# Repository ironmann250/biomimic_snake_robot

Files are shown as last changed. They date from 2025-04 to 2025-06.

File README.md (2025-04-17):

# biomimic_snake_robot
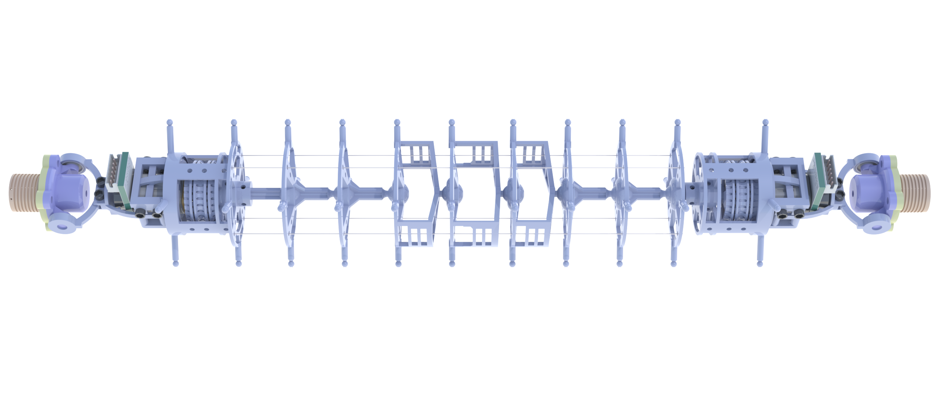
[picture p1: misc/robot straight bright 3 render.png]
biomimic_snake_robot render


CAD, PCB and Code files for an under actuated snake robot made to mimic snakes.

# Requirements
- Solidworks v2022
- python v3.8+ (anaconda packages)
- arduino (esp32 arduino api v3+)
- for V1 PCB code use stm32cubeide or similar ARM Dev IDE(like keil)
- EasyEDA PRO (PCB design)

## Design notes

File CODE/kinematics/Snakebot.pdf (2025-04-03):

# Snakebonnnnt

Munyakabera Jean Claude

September 2024

## 1 Definitions

S = Number of Segments
θn = Relative angle of segment n
Θn = Absolute angle of segment n
Cn = Center (base) point of segment n Ln = Left point of segment n
Rn = Right point of segment n
W = Width of segment from center to edge H = Height of segment from center to top X = Cord displacement (per segment)

Rot(

a
b

, θ) =
cosθ −sinθ

sinθ cosθ a b

(1)

=

a · cosθ − b · sinθ

a · sinθ + b · cosθ
(2)

## 2 Models

Θn =

X

S

i=0

θi | (3)

Cn+1 = Cn + Rot(

0
H
, Θn) | (4)

Ln = Cn − Rot(

W
0
, Θn) | (5)

Rn = Cn + Rot(

W
0
, Θn) | (6)

1

## 3 Initial Conditions

C0 =

0
0
(7)
θ0 = 0 | (8)

L0 = C0 − Rot(

W
0

, Θ0) =
−W
0
(9)

R0 = C0 + Rot(

W
0

, Θ0) =
W
0
(10)

C1 = C0 + Rot(

0
H

, Θ0) =
0
H
(11)

L1 = C1 − Rot(

W
0

, Θ) =
−W · cosΘ
H − W · sinΘ
(12)

R1 = C1 + Rot(

W
0

, Θ) =
W · cosΘ
H + W · sinΘ
(13)

## 4 Inverse solution

Let Θ = Θ1 for readability, then

∥L1 − L0∥2 = H − X | (14)
∥R1 − R0∥2 = H + X | (15)
∥R1 − R0∥2 = ∥L1 − L0∥ + 2X | (16)
W · cosΘ − W
H + W · sinΘ

2

=

W − W · cosΘ
H − W · sinΘ

2

+ 2X

p
(W · cosΘ − W)
2 + (H + W · sinΘ)² = | (17)
p
(W − W · cosΘ)² + (H − W · sinΘ)² + 2X | (18)

Apply two approximations for small angles:

cos(θ) = 1 −

θ

2
2

(19)

sin(θ) = θ | (20)
r
W² Θ⁴
4
+ H² + W²Θ² + 2HWΘ = | (21)
r
W² Θ⁴
4

+ H² + W²Θ² − 2HWΘ + 2X

2

Simplify further and remove terms that are negligible at small angles:

p

H² + 2HWΘ = p
H² − 2HWΘ + 2X | (22)

H² + 2HWΘ = H² − 2HWΘ + 4X(X +

p
H² − 2HWΘ) (23)

4HWΘ = 4X(X +

p
H² − 2HWΘ) | (24)
HWΘ ≈ X(X + H) | (25)

Θ ≈

X(X + H)
W H

(26)

3

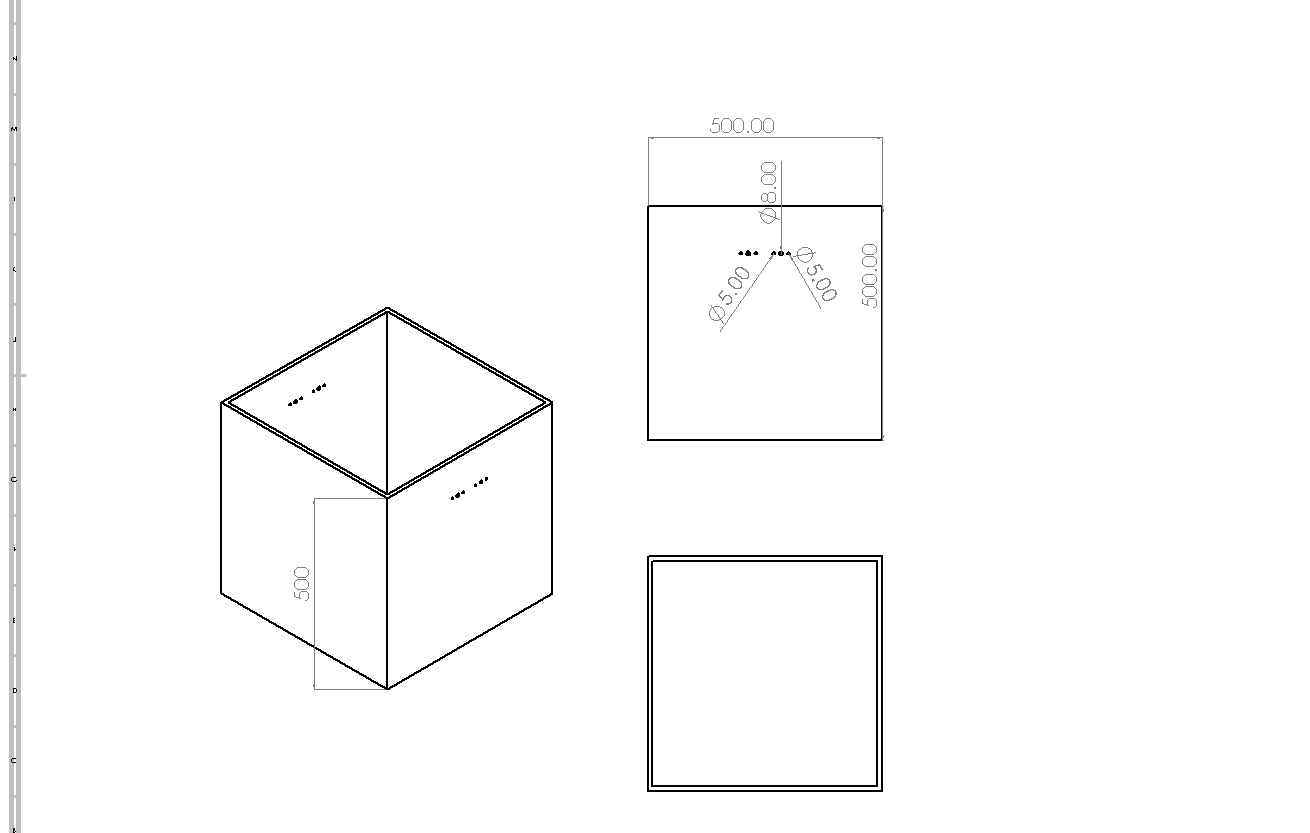
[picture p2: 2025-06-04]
CAD/V3/acrylic cube.TIF

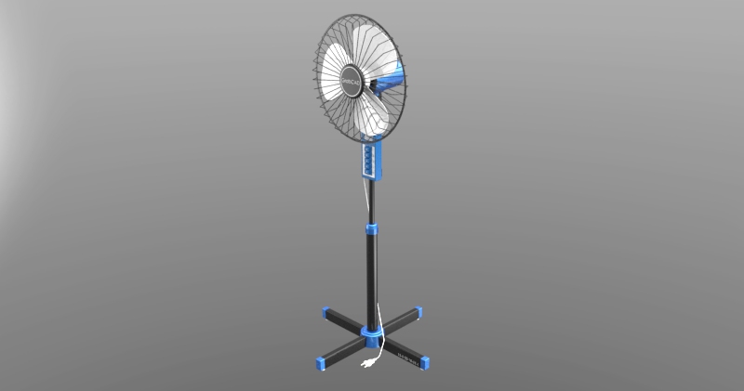
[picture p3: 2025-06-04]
CAD/V3/stand-fan-4/Sobni Ventilator (Rendering ).jpg

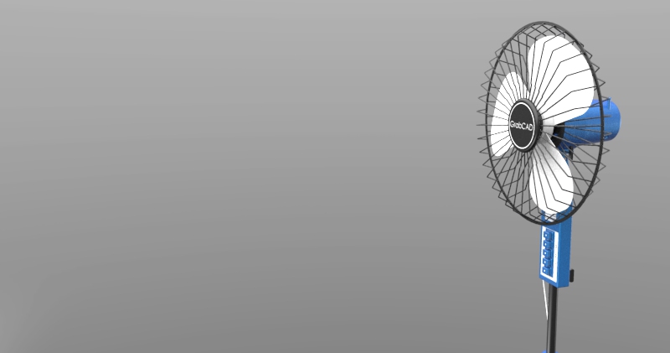
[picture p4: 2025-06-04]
CAD/V3/stand-fan-4/Sobni Ventilator (Rendering 4 ).jpg

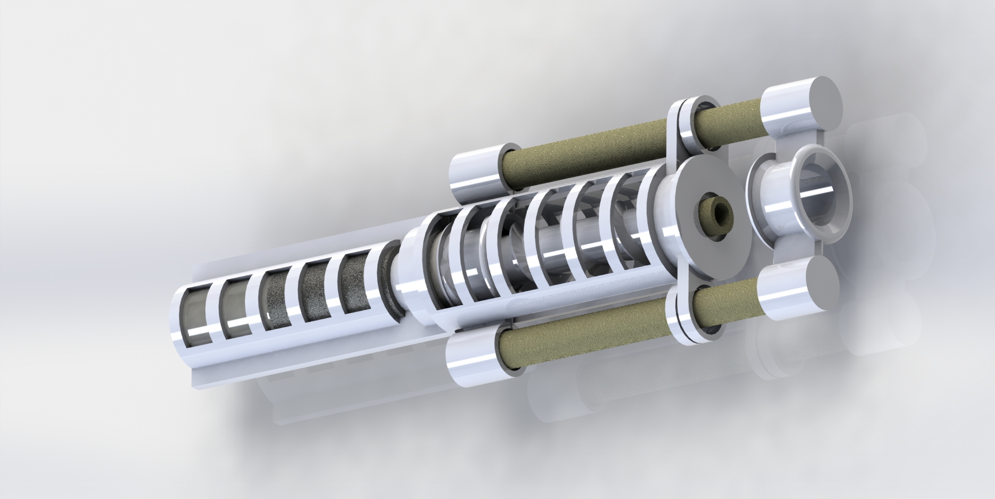
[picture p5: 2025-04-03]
CAD/modular version/linear motor render.JPG

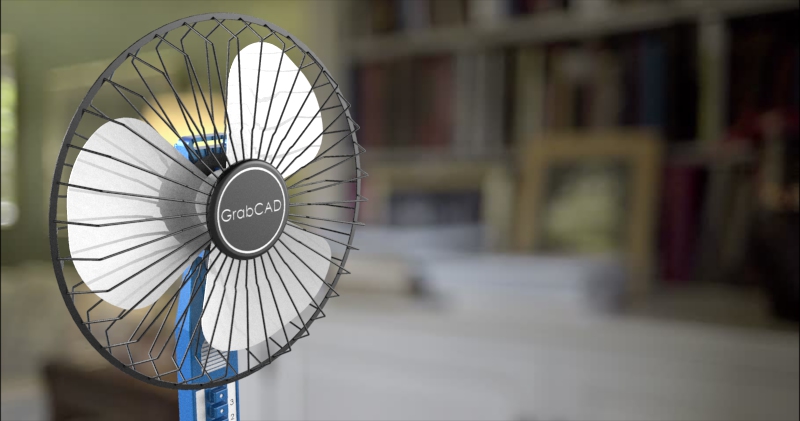
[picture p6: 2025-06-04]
CAD/V3/stand-fan-4/Sobni Ventilator (Rendering 3).jpg

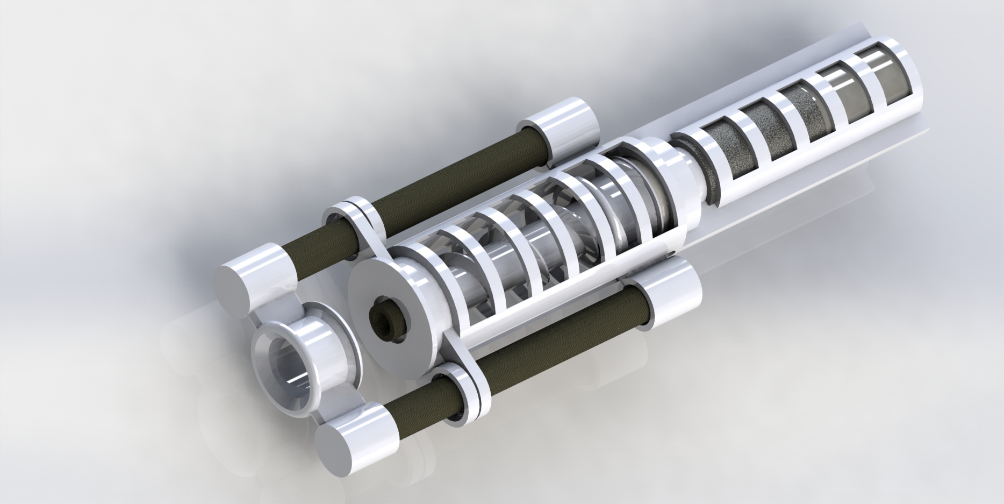
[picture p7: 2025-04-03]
CAD/modular version/linear motor render2.JPG

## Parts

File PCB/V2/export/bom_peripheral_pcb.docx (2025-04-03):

No. | Quantity | Comment | Designator | Footprint | Value | Manufacturer Part | Manufacturer | Supplier Part | Supplier
1 | 2 | 0.1uF | C1, C3 | C0603 | 0.1uF
2 | 4 | 10uF | C2, C4, C5, C6 | C0603 | 10uF
3 | 1 | DF40C-40DP-0.4V(51) | CN1_female1 | CONN-SMD_DF40C-40DP-0.4V | | DF40C-40DP-0.4V(51) | HRS(广濑) | C424643 | LCSC
4 | 1 | PMEG2010EPK,315 | D1 | SOD1608_L1.6-W0.8-LS1.6-RD | | PMEG2010EPK,315 | Nexperia(安世) | C552829 | LCSC
5 | 1 | AFC01-S08FCA-00 | FPC3 | FPC-SMD_P0.50-8P_FGS-XJ-H2.0 | | AFC01-S08FCA-00 | JS(钜硕电子) | C262657 | LCSC
6 | 1 | XL-1005UGC_C2856703 | LED1 | LED0402-RD_GREEN | | XL-1005UGC | XINGLIGHT(成兴光) | C2856703 | LCSC
7 | 1 | IRLML6401TRPBF | Q2 | SOT-23-3_L2.9-W1.3-P1.90-LS2.4-BR | | IRLML6401TRPBF | TECH PUBLIC(台舟) | C5182042 | LCSC
8 | 2 | IRLML6244TRPBF | Q5, Q6 | SOT-23-3_L2.9-W1.3-P1.90-LS2.4-BR | | IRLML6244TRPBF | Infineon(英飞凌) | C143946 | LCSC
9 | 1 | 5.1k | R1 | R0603 | 5.1k
10 | 1 | 4.7K | R3 | R0402 | 4.7k | RC0402FR-0710KL | YAGEO(国巨) | C60490 | LCSC
11 | 2 | 10K | R4, R5 | R0603 | 10K
12 | 2 | 1TS015A-1500-0600-CT | SW1, SW2 | SW-SMD_L3.0-W2.0-LS3.5 | | 1TS015A-1500-0600-CT | HYP(鸿源精密) | C319434 | LCSC
13 | 1 | DOUBLE_DRV8210 | U2 | DOUBLE_DRV8210
14 | 1 | SGM2212-3.3XKC3G/TR | U5 | SOT-223-4_L6.5-W3.5-P2.30-LS7.0-BR | | SGM2212-3.3XKC3G/TR | | C9900018517 | LCSC
15 | 1 | RED LED | U6 | LED0402-R-RD | | RED LED | YONGYUTAI(永裕泰) | C20608784 | LCSC
16 | 1 | MicroQTJ | USB1 | MICRO-USB-SMD_MICROQTJ-5P | | MicroQTJ | SHOU HAN(首韩) | C404968 | LCSC

BILL OF MATERIALS: PERIPHERAL PCB

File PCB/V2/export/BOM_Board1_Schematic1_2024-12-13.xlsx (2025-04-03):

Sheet: bom模板
 |  |  |  | Bill of Materials | BOM_Board1_Schematic1_2024-12-13
 |  |  |  | Project Title： | new pcb design
 |  |  |  | Variant:
 |  |  |  | Report Time： | 2024年12月13日 15:29:9
No. | Quantity | Comment | Designator | Footprint | Value | Manufacturer Part | Manufacturer | Supplier Part | Supplier | buy | solder
1 | 20 | Test-Point | 3V3, ADC1, ADC2, AO1, AO2, BO1, BO2, COM_5V, GND1, GND2, GND3, HEAT1, HEAT2, PWM4, RXD0, SCL1, SDA1, TXD0, VBAT, VM | Test-Point-0.5mm |  |  |  |  |  | 0 | û
2 | 2 | 0.1uF | C1, C3 | C0603 | 0.1uF |  |  |  |  | 30 | ü
3 | 4 | 10uF | C2, C4, C5, C6 | C0603 | 10uF |  |  |  |  | 50 | ü
4 | 1 | DF40C-40DP-0.4V(51) | CN1_female1 | CONN-SMD_DF40C-40DP-0.4V |  | DF40C-40DP-0.4V(51) | HRS(广濑) | C424643 | LCSC | 0 | ü
5 | 1 | PMEG2010EPK,315 | D1 | SOD1608_L1.6-W0.8-LS1.6-RD |  | PMEG2010EPK,315 | Nexperia(安世) | C552829 | LCSC | 0 | ü
6 | 1 | AFC01-S08FCA-00 | FPC3 | FPC-SMD_P0.50-8P_FGS-XJ-H2.0 |  | AFC01-S08FCA-00 | JS(钜硕电子) | C262657 | LCSC | 15 | ü
7 | 1 | XL-1005UGC_C2856703 | LED1 | LED0402-RD_GREEN |  | XL-1005UGC | XINGLIGHT(成兴光) | C2856703 | LCSC | 15 | ü
8 | 1 | IRLML6401TRPBF | Q2 | SOT-23-3_L2.9-W1.3-P1.90-LS2.4-BR |  | IRLML6401TRPBF | TECH PUBLIC(台舟) | C5182042 | LCSC | 0 | ü
9 | 2 | IRLML6244TRPBF | Q5, Q6 | SOT-23-3_L2.9-W1.3-P1.90-LS2.4-BR |  | IRLML6244TRPBF | Infineon(英飞凌) | C143946 | LCSC | 0 | ü
10 | 1 | 5.1k | R1 | R0603 | 5.1k |  |  |  |  | 15 | ü
11 | 1 | 4.7K | R3 | R0402 |  | RC0402FR-0710KL | YAGEO(国巨) | C60490 | LCSC | 15 | ü
12 | 2 | 10K | R4, R5 | R0603 | 10K |  |  |  |  | 25 | ü
13 | 2 | 1TS015A-1500-0600-CT | SW1, SW2 | SW-SMD_L3.0-W2.0-LS3.5 |  | 1TS015A-1500-0600-CT | HYP(鸿源精密) | C319434 | LCSC | 0 | ü
14 | 1 | DOUBLE_DRV8210 | U2 | DOUBLE_DRV8210 |  |  |  |  |  | 0 | û
15 | 1 | SGM2212-3.3XKC3G/TR | U5 | SOT-223-4_L6.5-W3.5-P2.30-LS7.0-BR |  | SGM2212-3.3XKC3G/TR |  | C9900018517 | LCSC | 0 | ü
16 | 1 | RED LED | U6 | LED0402-R-RD |  | RED LED | YONGYUTAI(永裕泰) | C20608784 | LCSC | 15 | ü
17 | 1 | MicroQTJ | USB1 | MICRO-USB-SMD_MICROQTJ-5P |  | MicroQTJ | SHOU HAN(首韩) | C404968 | LCSC | 0 | ü

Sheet: Field汇总
Project Title | new pcb design
Borard Title | Board1
Schematic Title | Schematic1
PCB Title
Variant Name
Total Quantity | 43
Report Time | 15:29:9
Report Date | 2024年12月13日
Report Date&Time | 2024年12月13日 15:29:9
File Name | BOM_Board1_Schematic1_2024-12-13
Filter Option | <Parameter filter option not found>

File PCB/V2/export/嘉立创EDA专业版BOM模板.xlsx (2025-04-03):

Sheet: bom模板
 |  |  |  | Bill of Materials | Field=File Name
 |  |  |  | Project Title： | Field=Project Title
 |  |  |  | Variant: | Field=Variant Name
 |  |  |  | Report Time： | Field=ReportDateTime
No. | Column=Quantity | Column=Comment | Column=Designator | Column=Footprint | Column=Value | Column=Manufacturer Part | Column=Manufacturer | Column=Supplier Part | Column=Supplier | Column=LCSC Price | Total
1 |  |  |  |  |  |  |  |  |  |  | ¥0.00
2 |  |  |  |  |  |  |  |  |  |  | ¥0.00
3 |  |  |  |  |  |  |  |  |  |  | ¥0.00
4 | ¥0.00

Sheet: Field汇总
Project Title | Field=Project Title
Borard Title | Field=Borard Title
Schematic Title | Field=Schematic Title
PCB Title | Field=PCB Title
Variant Name | Field=Variant Name
Total Quantity | Field=Total Quantity
Report Time | Field=Report Time
Report Date | Field=Report Date
Report Date&Time | Field=ReportDateTime
File Name | Field=File Name
Filter Option | Field=Filter Option

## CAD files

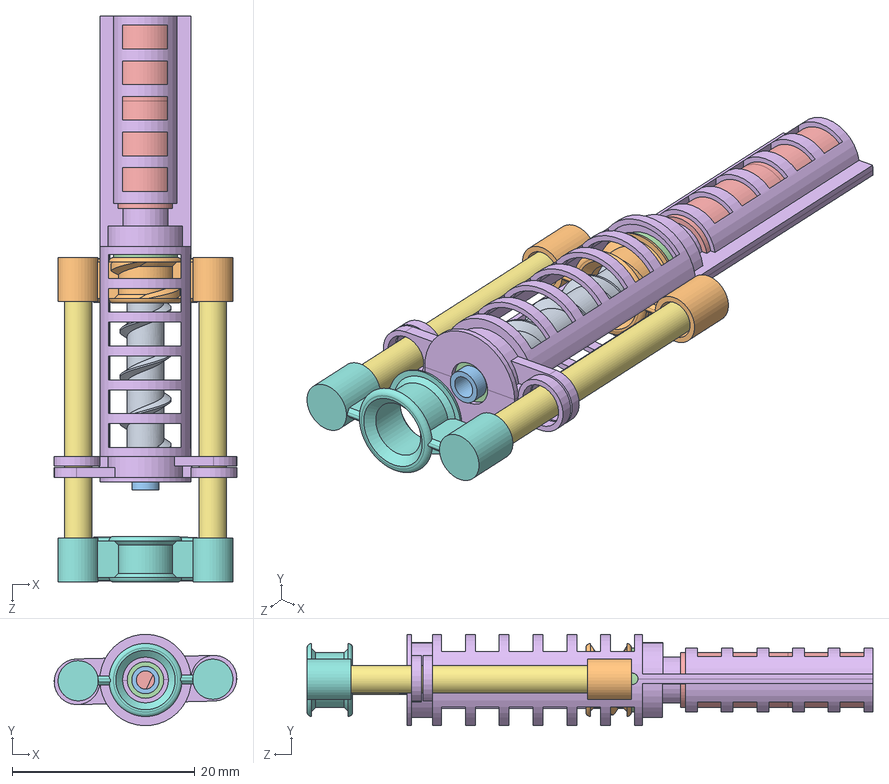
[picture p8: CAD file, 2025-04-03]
CAD/modular version/teeeeest.SLDASM
20.0 x 9.98 x 61.9 mm
screeeeeeeew
screw thingie
carbon fiber back
bearing x 2
motor
carbon fiber back 2.5MM x 2
CAP

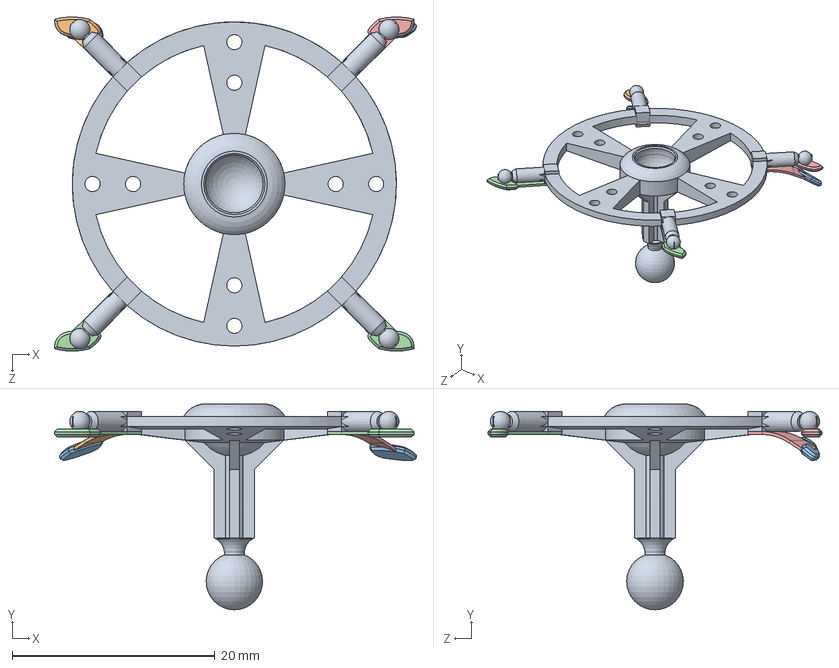
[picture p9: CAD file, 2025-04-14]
CAD/renders/foot bending assembly.SLDASM
35.7 x 20.3 x 33.0 mm
vertebrae v4
foot bent opposite
foot bent silicone part x 2
foot x 2
foot bent

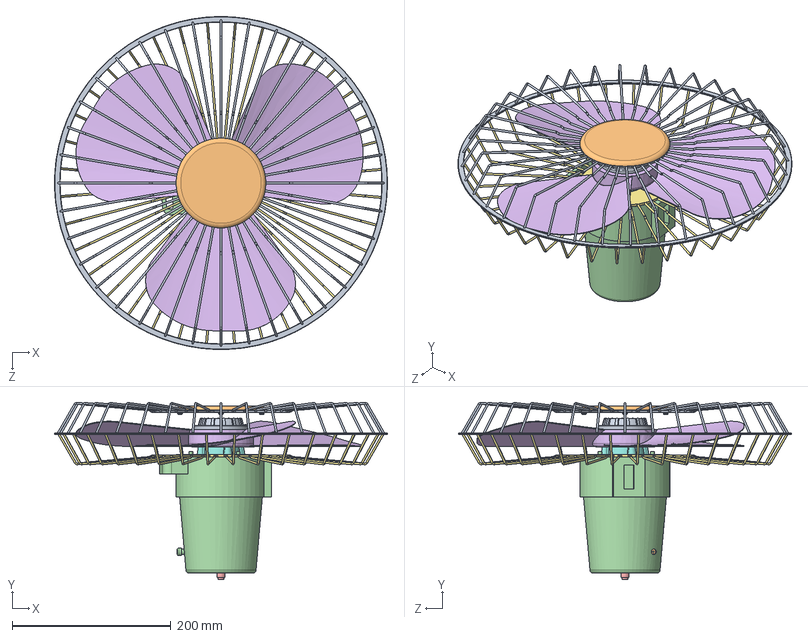
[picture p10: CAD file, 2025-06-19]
CAD/V3/stand-fan-4/Pod-sklop 3.SLDASM
419.0 x 222.7 x 419.0 mm
Resetka
Poklopac
Navrtka 2 x 4
Kuciste
Propeler
Resetka 2
Mali deo Ventilatora 5
Mali deo Ventilatora 4
Poluga

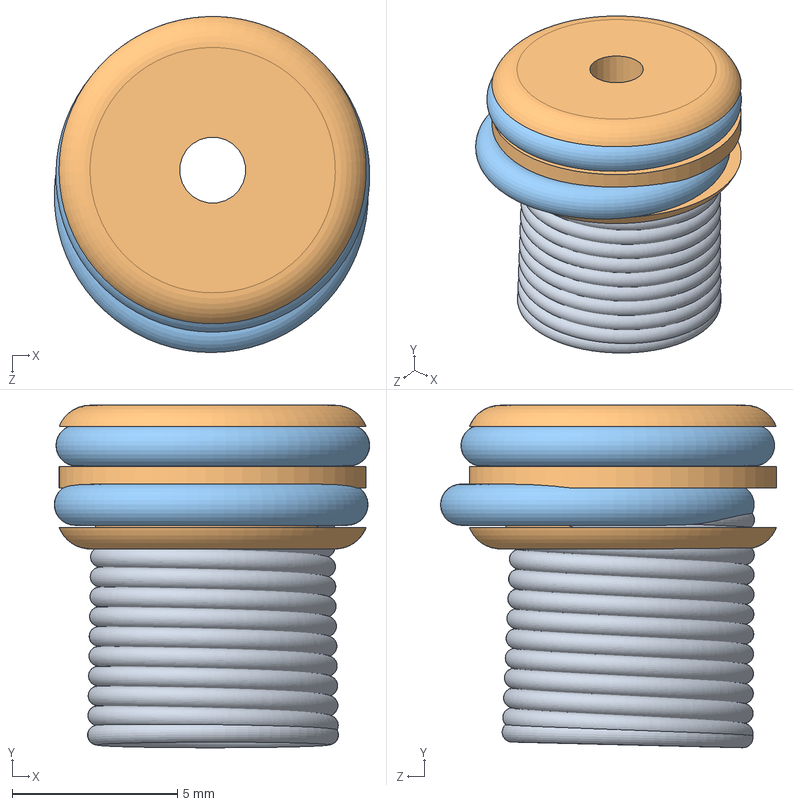
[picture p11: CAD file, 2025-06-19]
CAD/V3/snake_flyer/programmable adhesive assembly 2.SLDASM
9.55 x 10.4 x 10.2 mm
0.6_7_8_32 compressedSLDPRT
piston
9mm o ring x 2

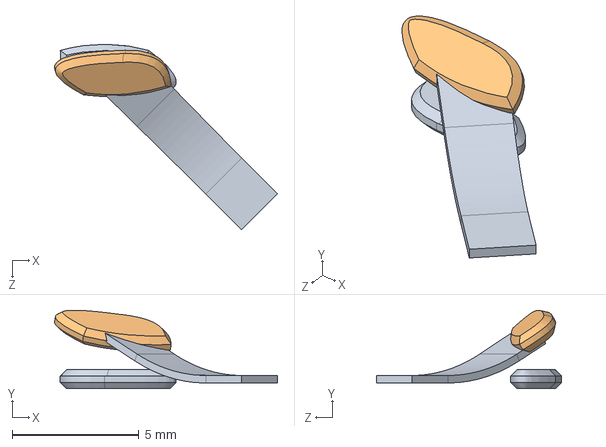
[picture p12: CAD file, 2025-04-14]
CAD/renders/foot bent opposite.SLDASM
8.81 x 3.10 x 7.33 mm
foot bent
foot bent silicone part

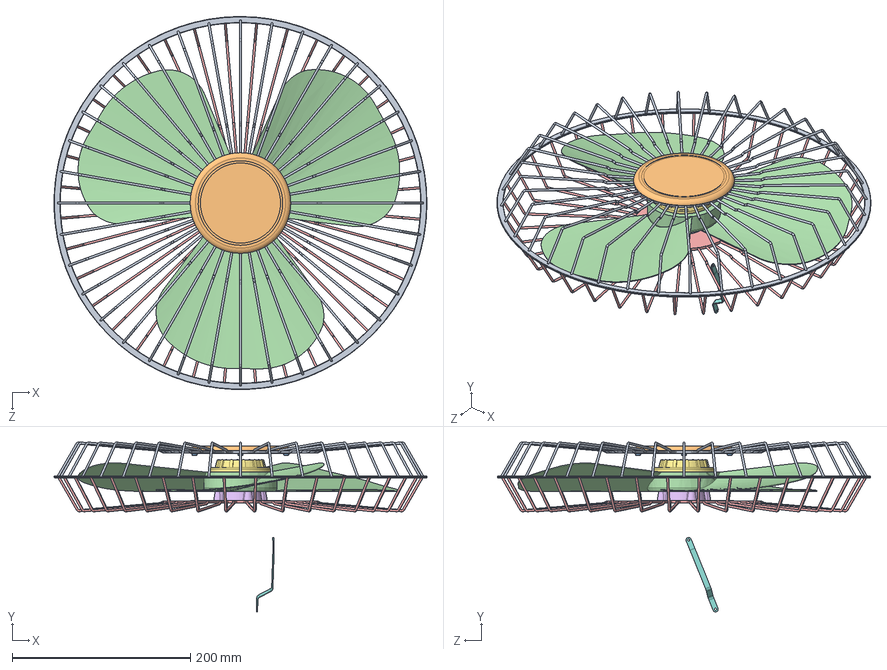
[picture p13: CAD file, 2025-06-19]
CAD/V3/stand-fan-4/Ventilator only.SLDASM
419.0 x 190.8 x 419.0 mm
Resetka
Poklopac
Navrtka 2 x 4
Propeler
Resetka 2
Mali deo Ventilatora 5
Mali deo Ventilatora 4
Poluga

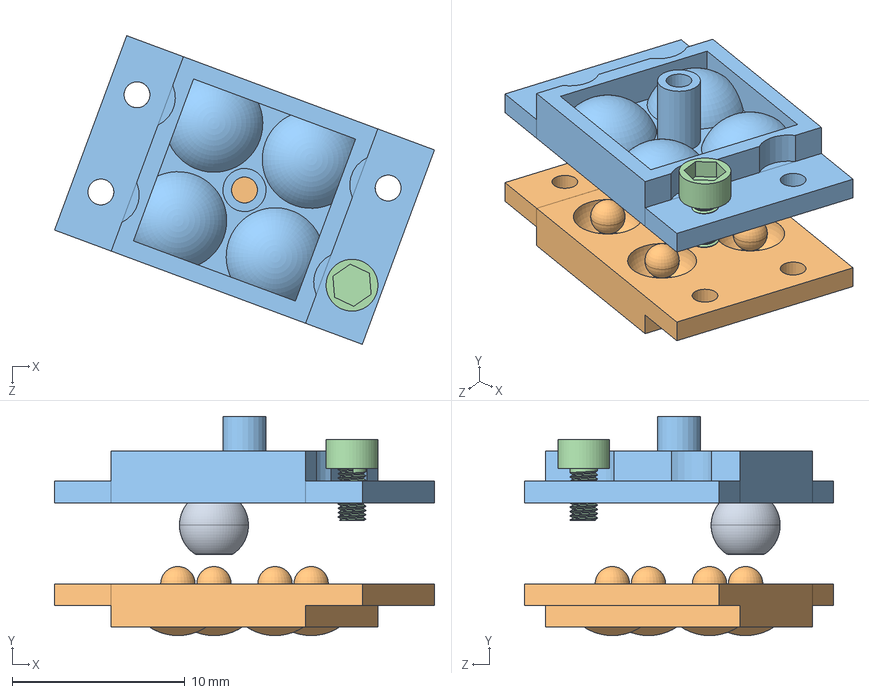
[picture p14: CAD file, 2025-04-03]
CAD/foot_mold/silicone foot mold v1.SLDASM
22.0 x 12.7 x 17.9 mm
Parting Line3[1]
Tooling Split1[1]
Tooling Split1[2]
3-1.6 screw

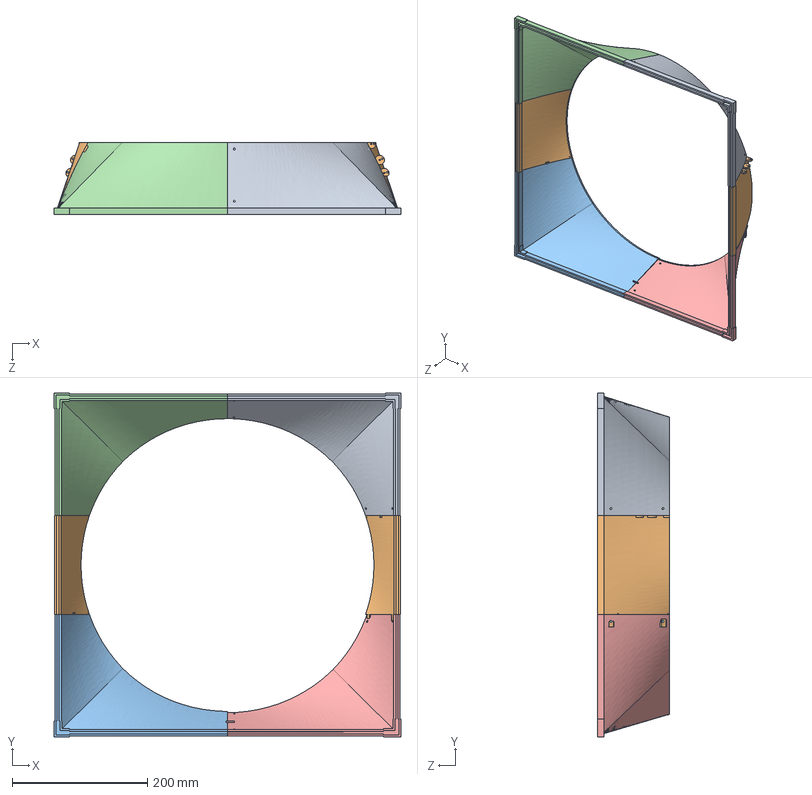
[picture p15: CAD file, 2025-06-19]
CAD/V3/circular-to-square.SLDASM
512.8 x 507.9 x 107.0 mm
circular-to-square_adapter_right
circular-to-square_adapter_middle x 2
circular-to-square_adapter_right_hole
circular-to-square_adapter_left_hole
circular-to-square_adapter_left

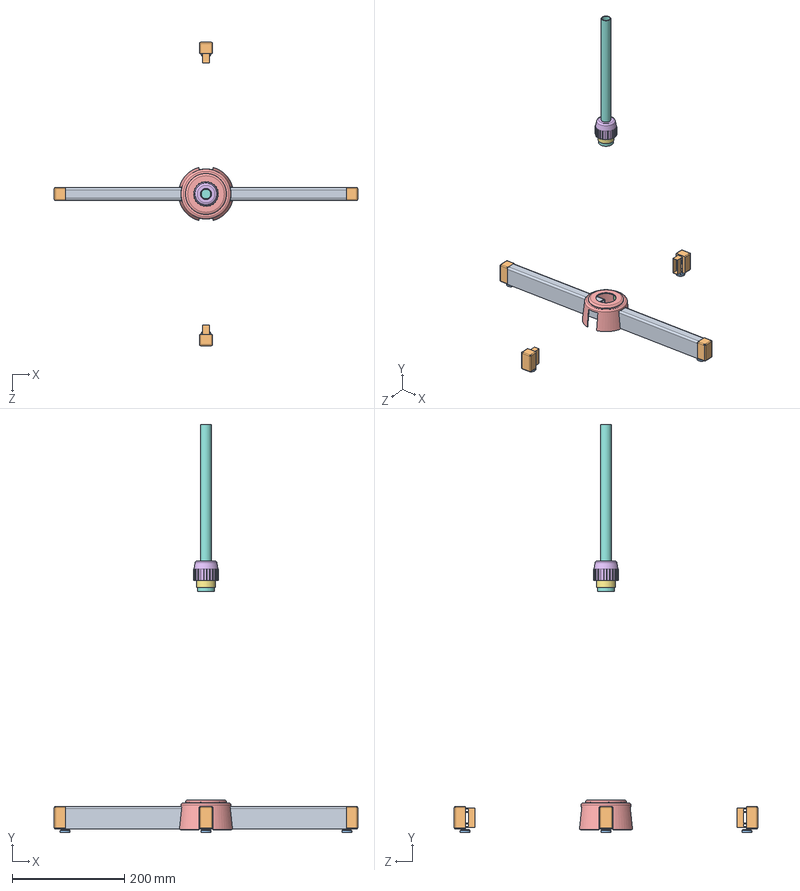
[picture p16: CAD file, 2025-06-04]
CAD/V3/stand-fan-4/Pod-sklop 1.SLDASM
540.0 x 725.9 x 540.0 mm
Dug metalni deo 2
Deo Ventilatora 1 x 4
Mali deo Ventilatora 2 x 4
Vijak x 4
Mali poklopac
Cep
Mali deo Ventilatora 3
Cev 2

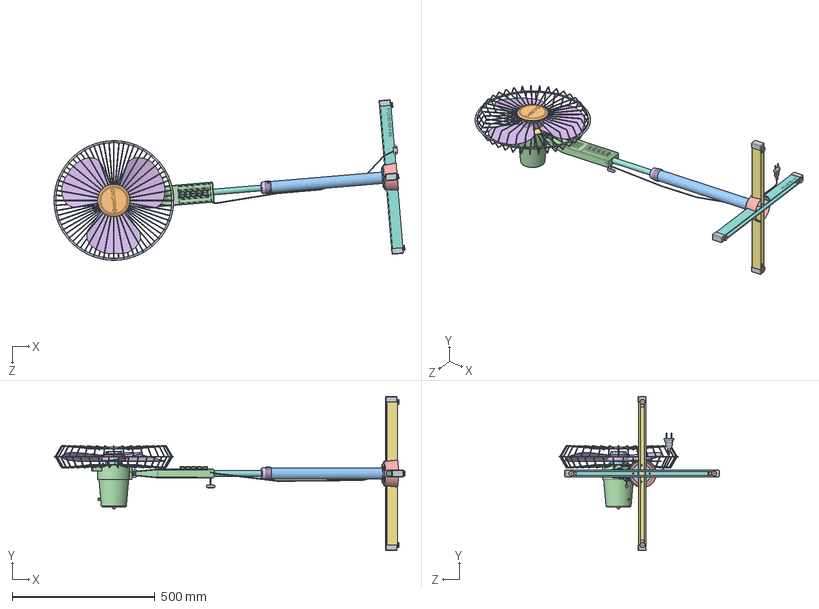
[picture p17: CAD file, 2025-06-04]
CAD/V3/stand-fan-4/Ventilator (Sklop) [GC].SLDASM
1228.7 x 540.0 x 562.3 mm
Resetka
Poklopac
Navrtka 2 x 4
Kuciste
Propeler
Resetka 2
Mali deo Ventilatora 5
Mali deo Ventilatora 4
Poluga
Podloska
Daljinski
Navrtka
Rucka x 2
Dug metalni deo 1
Dug metalni deo 2
Deo Ventilatora 1 x 4
Mali deo Ventilatora 2 x 4
Cev 1
Vijak x 4
Mali poklopac
Cep
Mali deo Ventilatora 3
Cev 2
Utikac

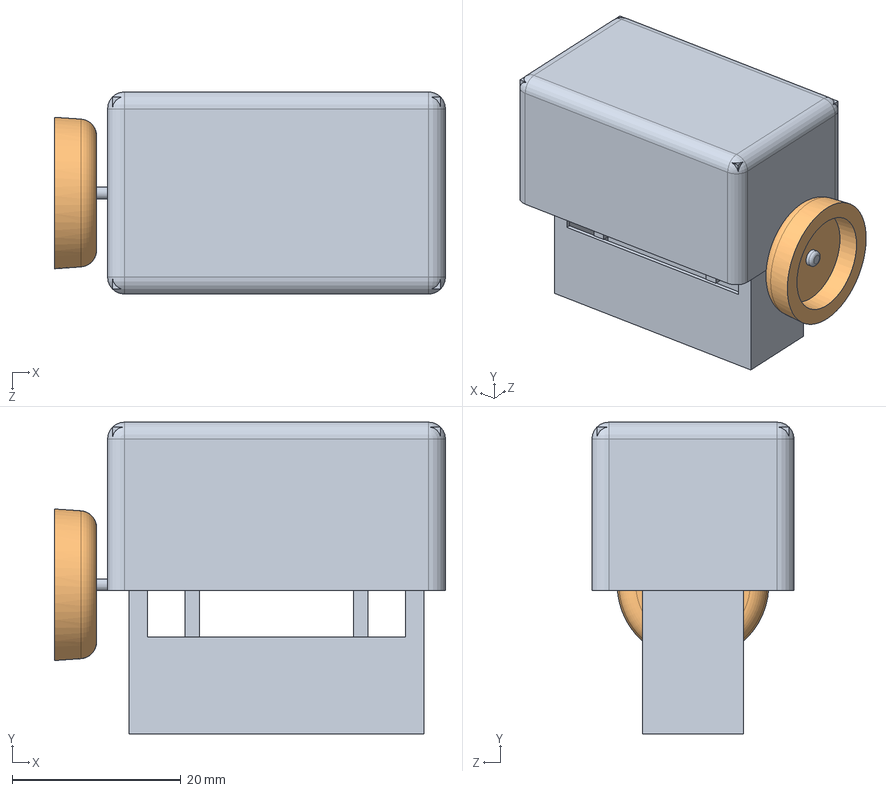
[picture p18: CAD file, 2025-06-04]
CAD/V3/stand-fan-4/Pod-sklop 2.SLDASM
46.4 x 37.0 x 24.0 mm
Deo Ventilatora 1
Mali deo Ventilatora 2

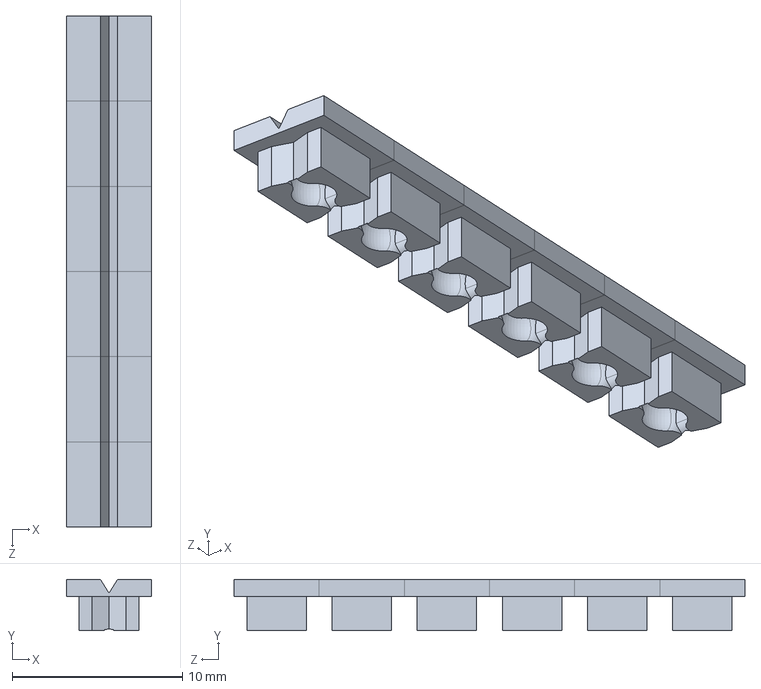
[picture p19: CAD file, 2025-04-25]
CAD/foot_mold/foot mold v4.SLDPRT
5.00 x 3.00 x 30.0 mm

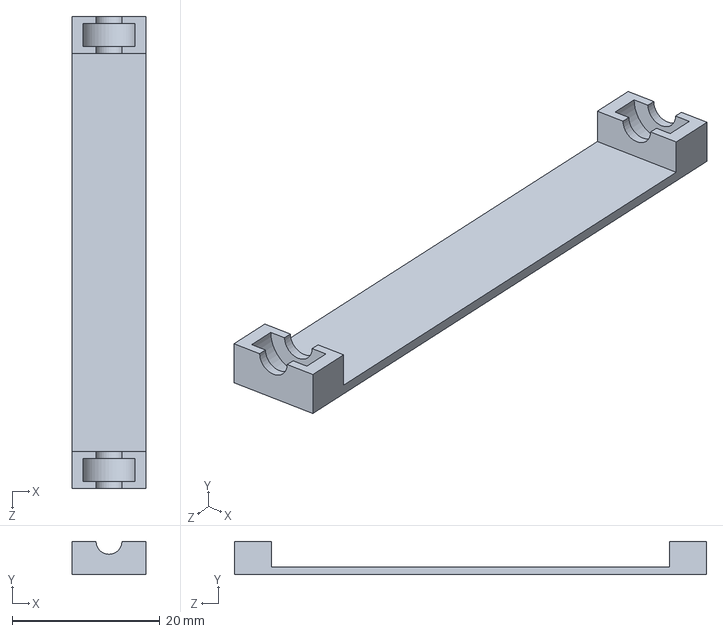
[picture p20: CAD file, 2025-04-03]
CAD/modular version/Backup of baseeeee.SLDPRT
10.0 x 4.50 x 64.0 mm

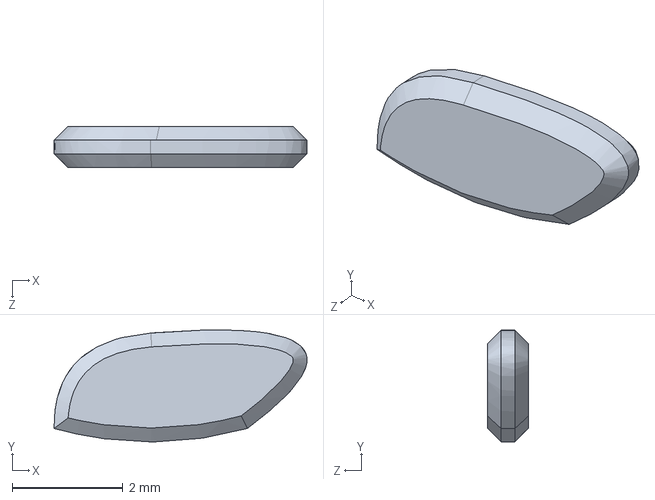
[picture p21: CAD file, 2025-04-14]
CAD/renders/foot bent silicone part.SLDPRT
4.58 x 2.02 x 0.75 mm

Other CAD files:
CAD/renders/bent foot assembly.SLDASM
CAD/V3/programmable adhesive assembly 2.SLDASM
CAD/modular version/Backup of teeeeest.SLDASM
CAD/skin_rough_mold/cylinder.SLDPRT
CAD/V1/5-2-2 encoder magnet'.SLDPRT
CAD/V1/623 zr02-ptfe bearing 3-10-4.SLDPRT
CAD/V1/back body 25mm.SLDPRT
CAD/V1/back support.SLDPRT
CAD/V1/body 25mm.SLDPRT
CAD/V1/encoder board circuit 0.8mm.SLDASM
CAD/V1/encoder board updated.SLDPRT
CAD/V1/k20 8mm motor.SLDPRT
CAD/V1/linear pulley 8 mm motor drive assembly.SLDASM
CAD/V1/middle vertebrae.SLDPRT
CAD/V1/pulley 8mm to bearing.SLDPRT
CAD/V1/vertebrae v4.SLDPRT
CAD/V1/winch 8mm to bearing.SLDPRT
CAD/V2/0.6_7_8_32 compressedSLDPRT.SLDPRT
CAD/V2/3-1.6 screw.SLDPRT
CAD/V2/9mm o ring.SLDPRT
CAD/V2/back body 25mm 2.SLDPRT
CAD/V2/bearing holder.SLDPRT
CAD/V2/bottom cover v2.SLDPRT
CAD/V2/bottom part.SLDPRT
CAD/V2/front body 25mm.SLDPRT
CAD/V2/heating module.SLDPRT
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

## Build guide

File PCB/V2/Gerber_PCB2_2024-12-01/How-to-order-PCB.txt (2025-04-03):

How to Order PCB

Please refer to:
https://prodocs.easyeda.com/en/pcb/order-order-pcb/index.html

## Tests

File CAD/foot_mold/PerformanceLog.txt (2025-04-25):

Number of Contacts: 5
Number of contact data: 310

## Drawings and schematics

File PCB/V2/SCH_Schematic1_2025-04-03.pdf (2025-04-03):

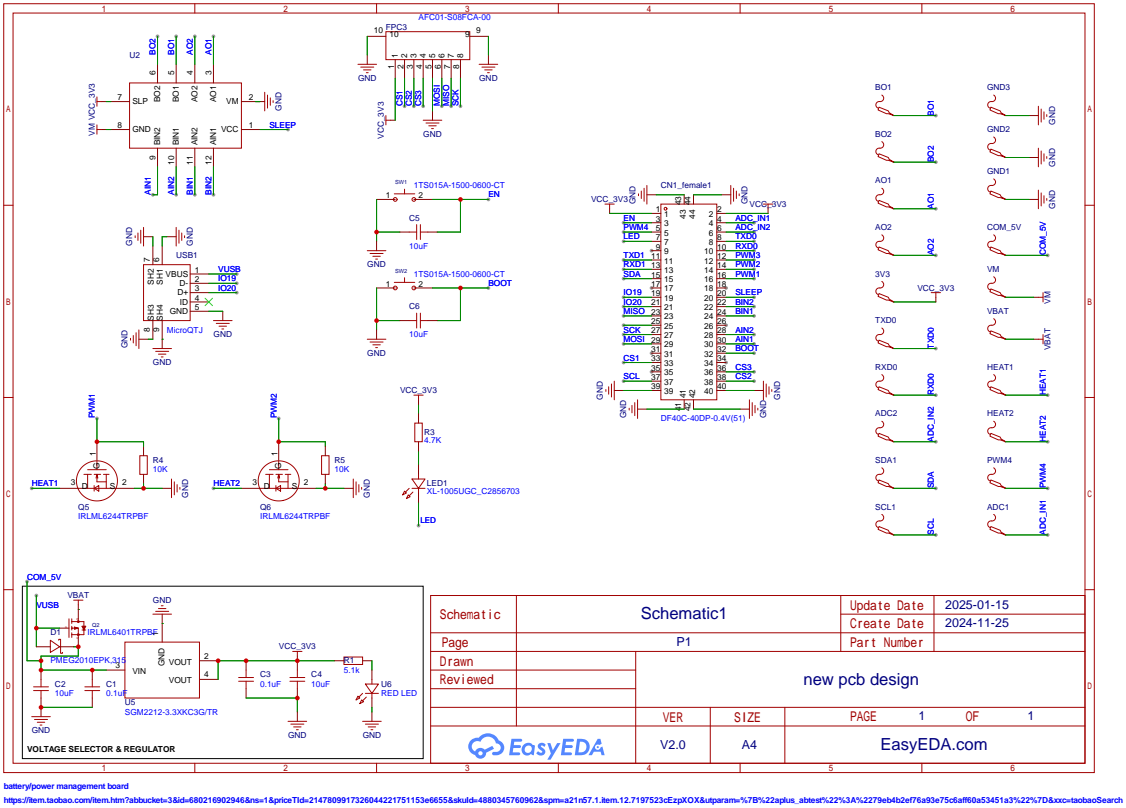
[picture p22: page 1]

battery/power management board
https://item.taobao.com/item.htm?id=680216902946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

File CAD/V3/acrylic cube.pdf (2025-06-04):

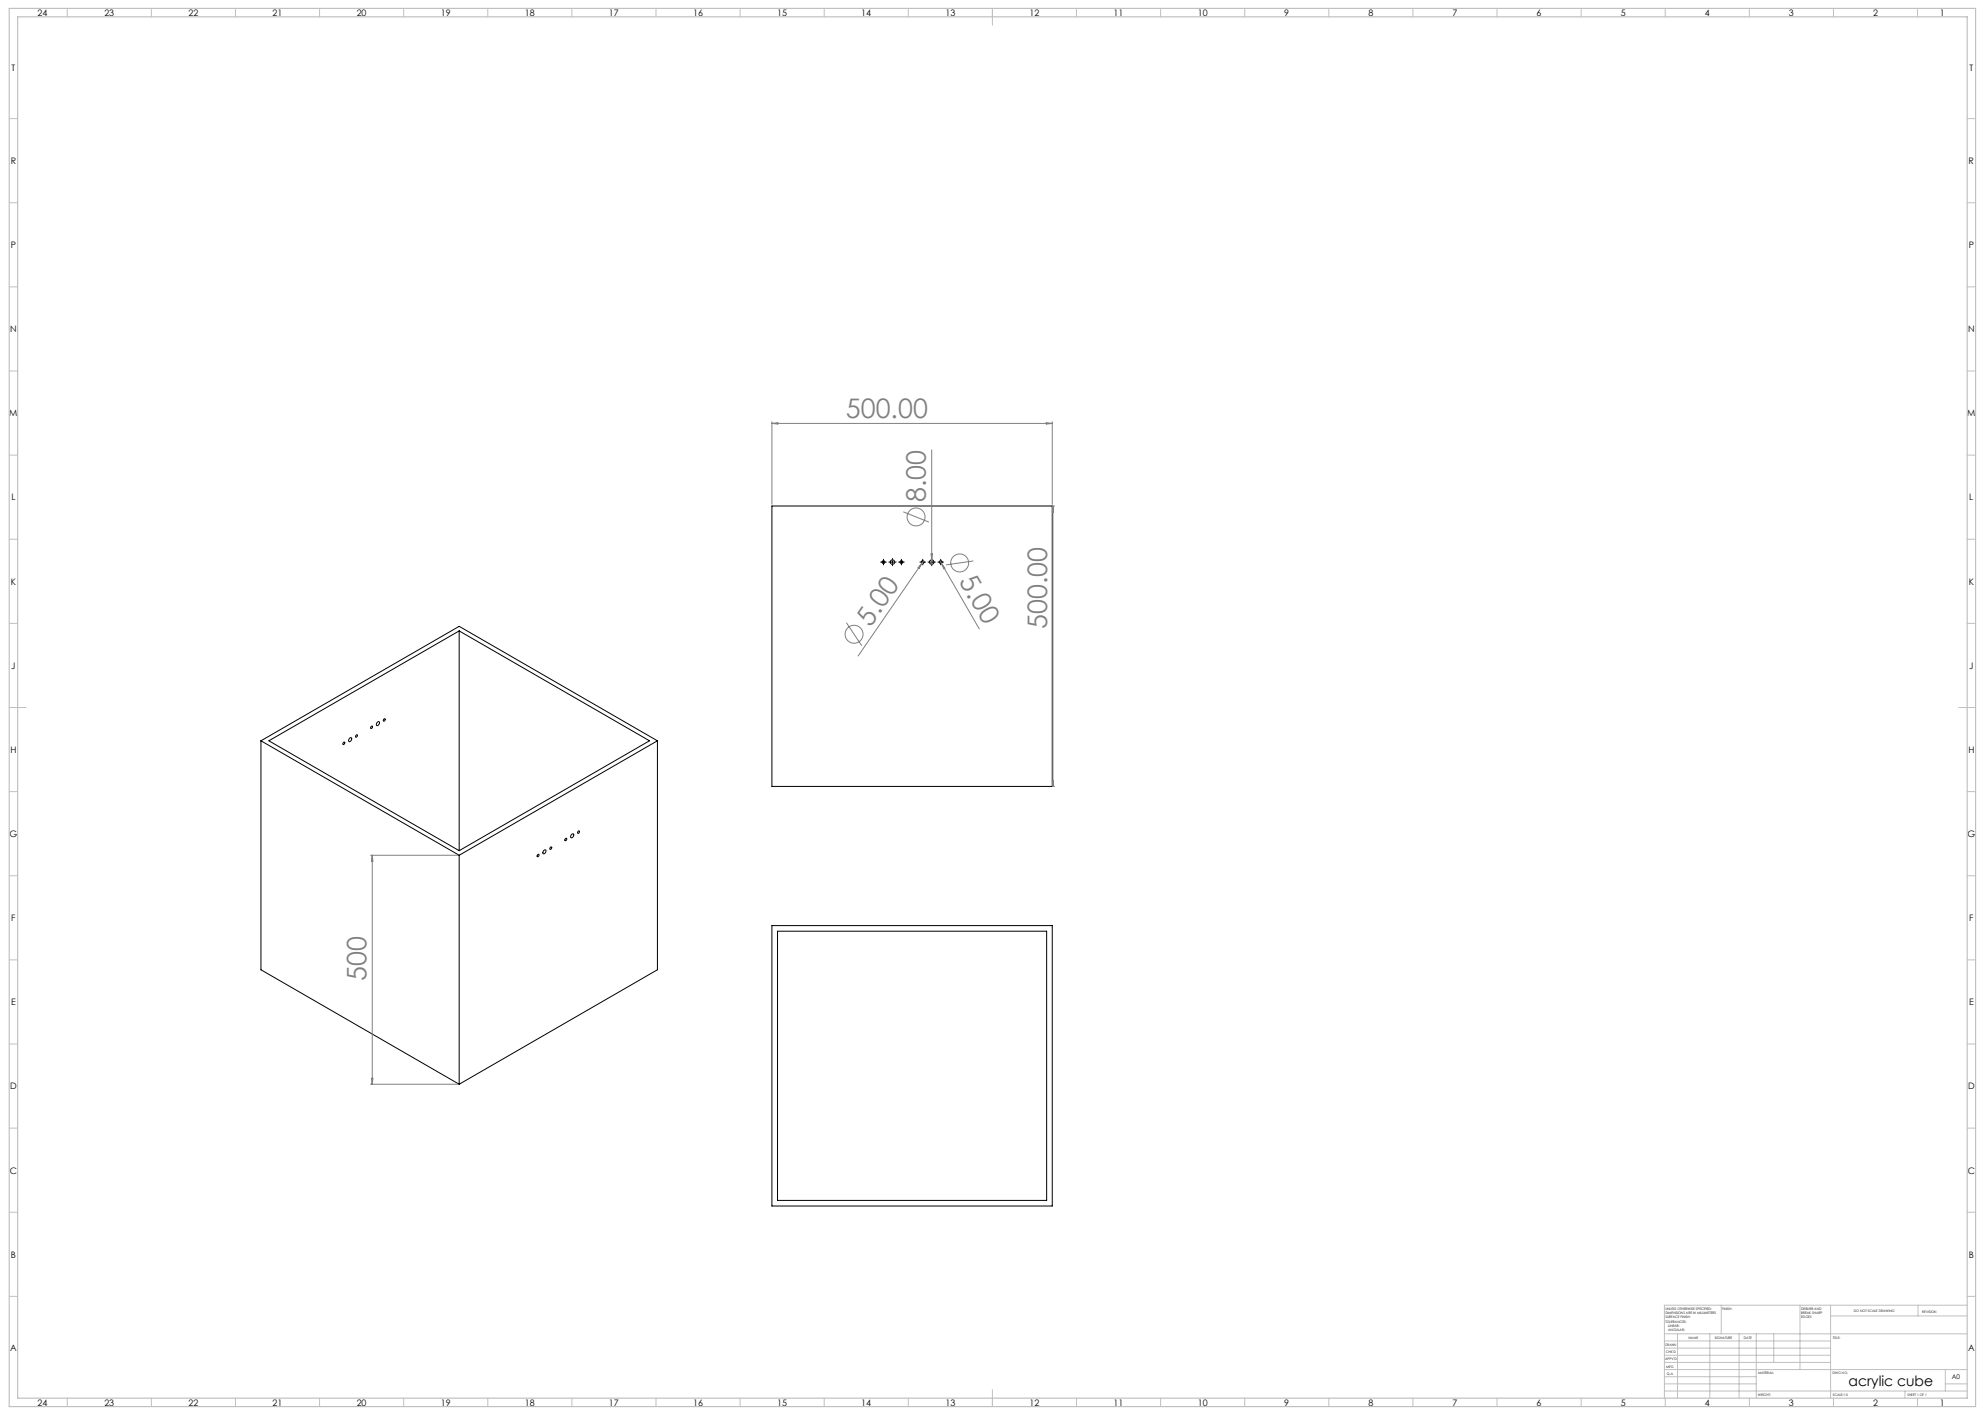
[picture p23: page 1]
FINISH:; DEBURR AND; BREAK SHARP; DO NOT SCALE DRAWING; REVISION; SCALE:1:5; SHEET 1 OF 1

UNLESS OTHERWISE SPECIFIED:
DIMENSIONS ARE IN MILLIMETERS
SURFACE FINISH:
TOLERANCES:
LINEAR:
ANGULAR:

NAME | SIGNATURE | DATE | | | | TITLE:

DRAWN
CHK'D
APPV'D
MFG
Q.A | | | | MATERIAL: | DWG NO. acrylic cube | A0

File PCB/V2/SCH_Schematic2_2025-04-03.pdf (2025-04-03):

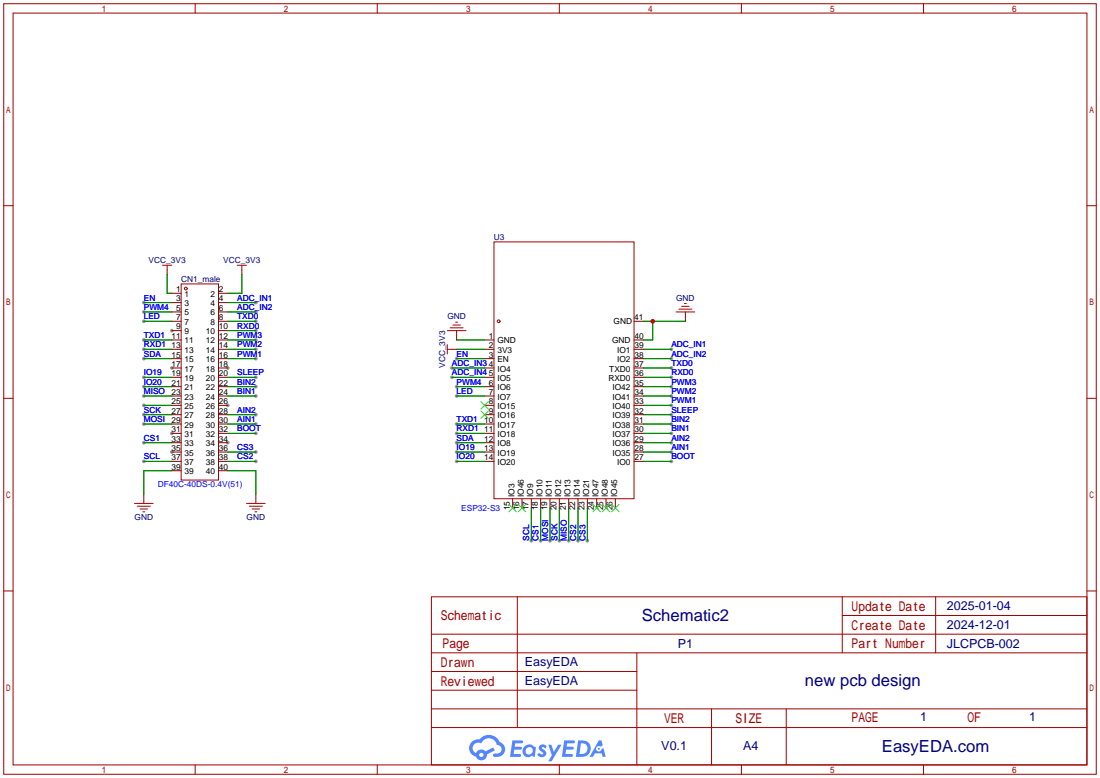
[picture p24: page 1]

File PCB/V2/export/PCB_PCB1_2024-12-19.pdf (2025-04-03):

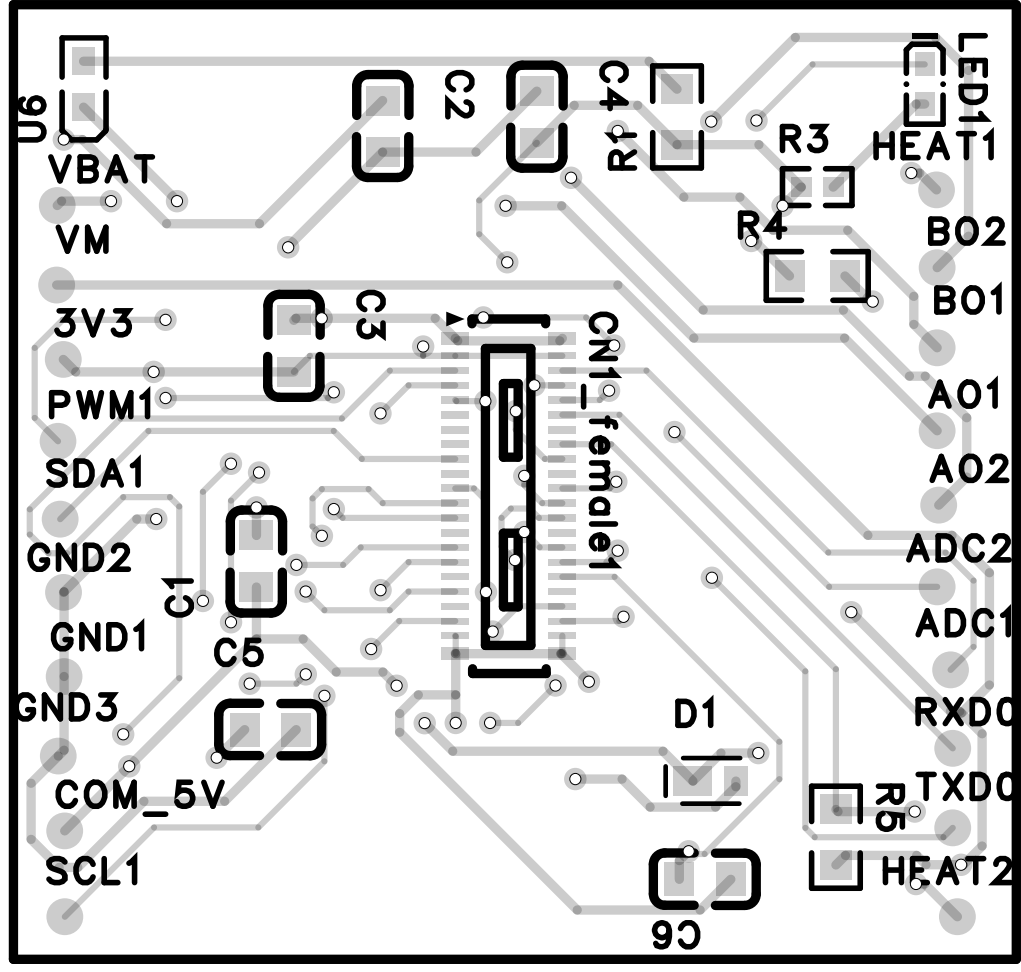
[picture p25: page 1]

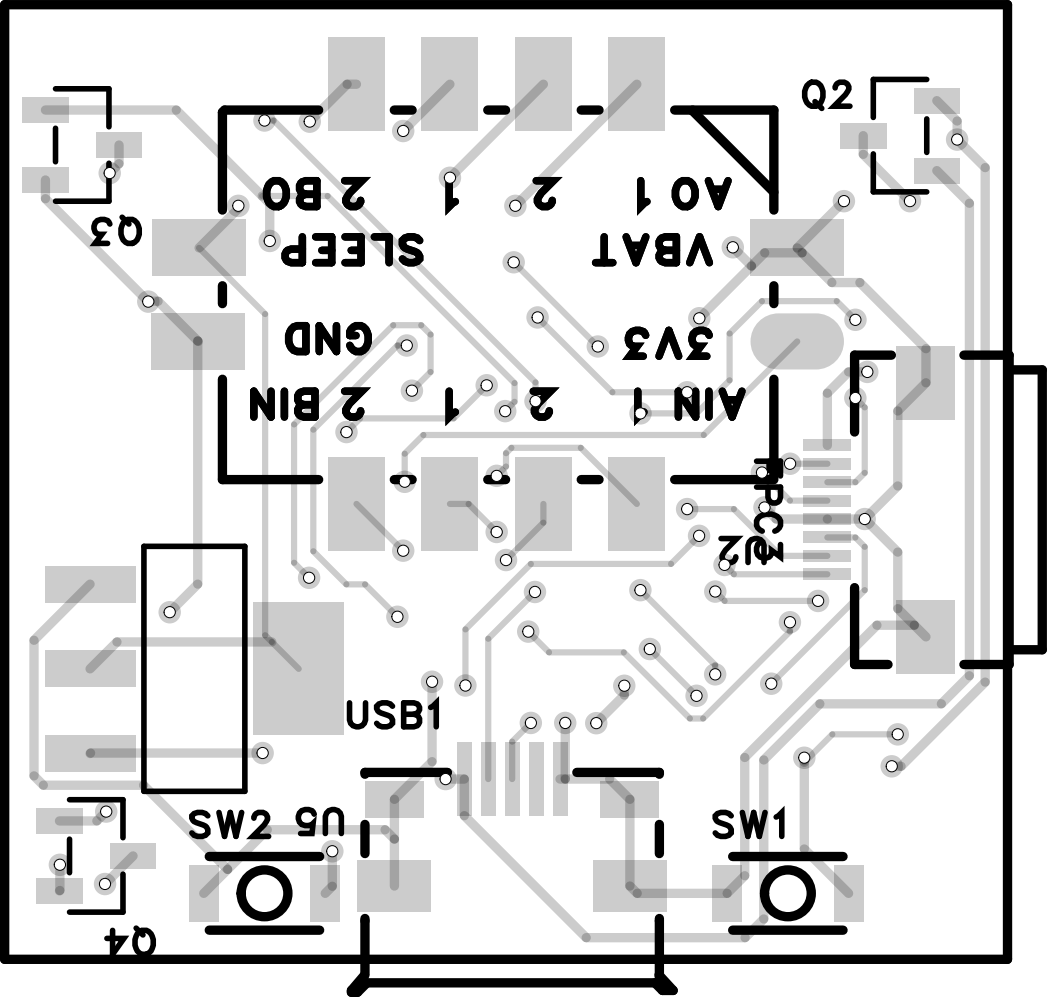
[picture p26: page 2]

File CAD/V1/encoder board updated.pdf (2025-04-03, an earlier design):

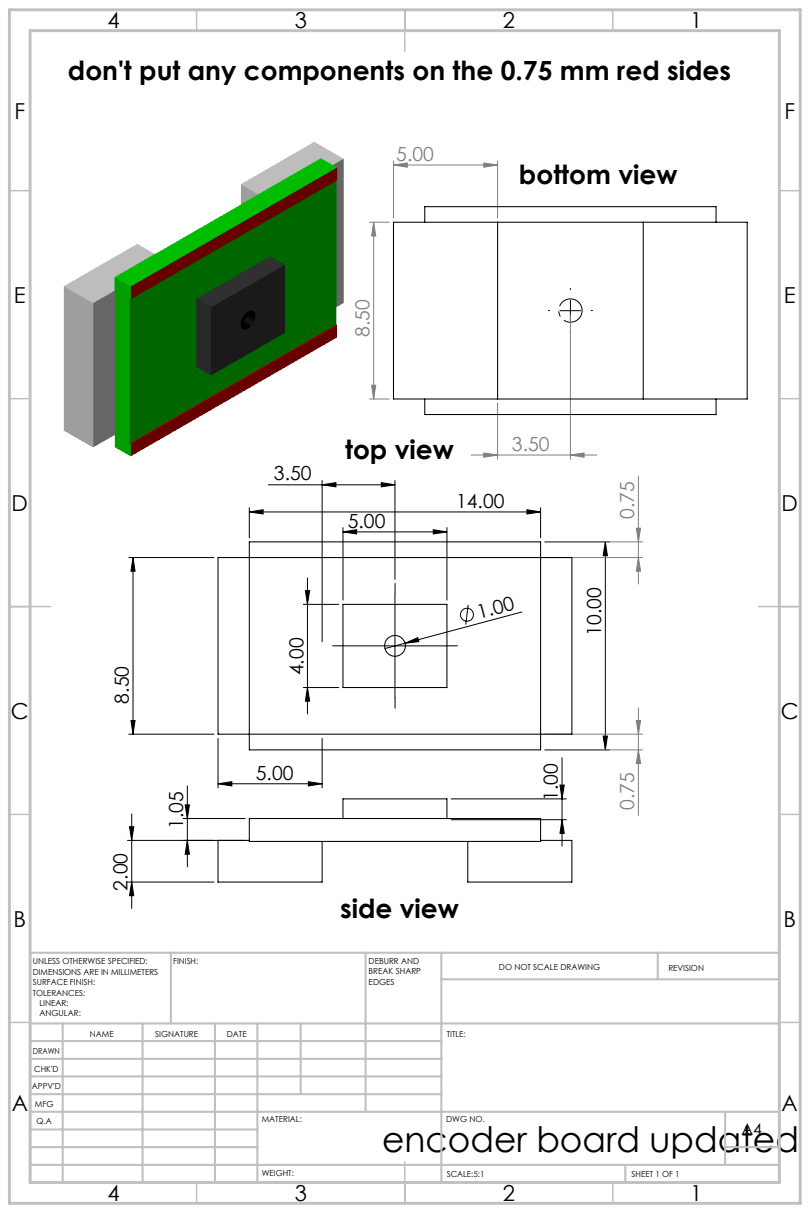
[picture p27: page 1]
bottom view; top view; side view; FINISH:; DEBURR AND; BREAK SHARP; DO NOT SCALE DRAWING; REVISION; SCALE:5:1; SHEET 1 OF 1

don't put any components on the 0.75 mm red sides

UNLESS OTHERWISE SPECIFIED:
DIMENSIONS ARE IN MILLIMETERS
SURFACE FINISH:
TOLERANCES:
LINEAR:
ANGULAR:

NAME | SIGNATURE | DATE | | | | TITLE:

DRAWN
CHK'D
APPV'D
MFG
Q.A | | | | MATERIAL: encoder board updated | DWG NO. | A4

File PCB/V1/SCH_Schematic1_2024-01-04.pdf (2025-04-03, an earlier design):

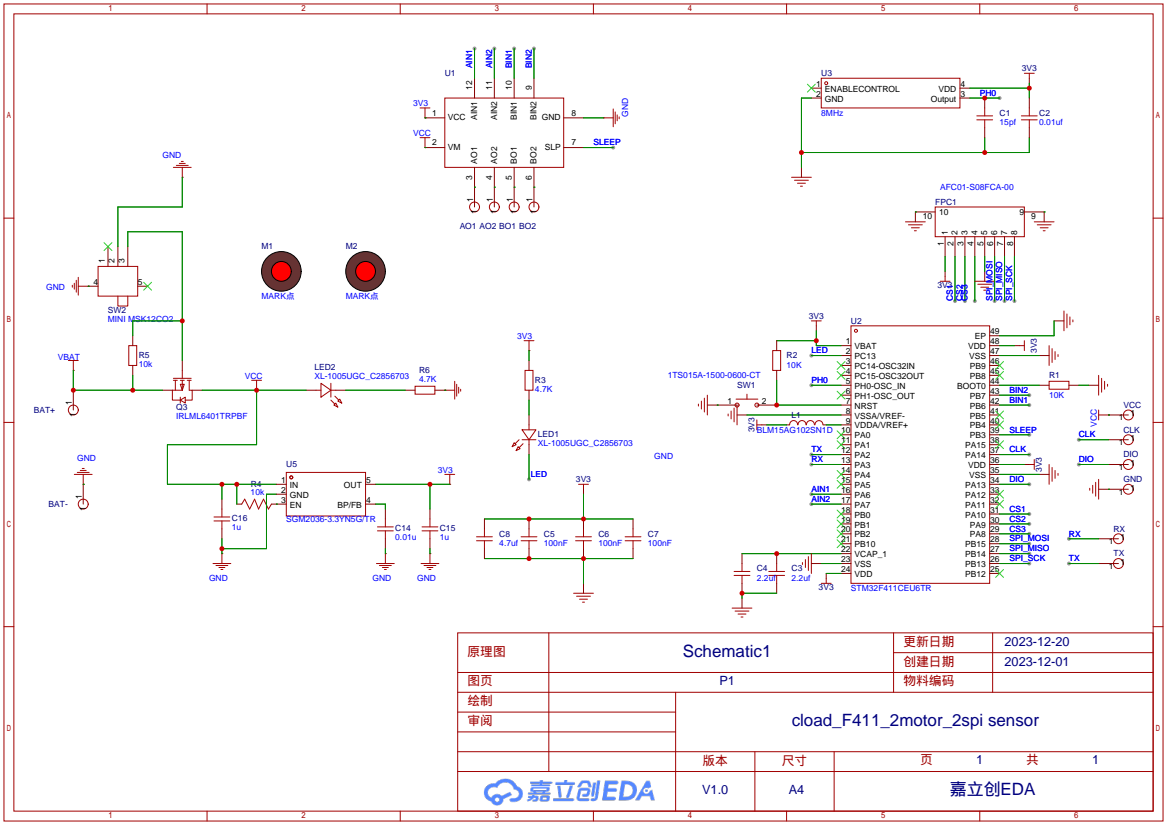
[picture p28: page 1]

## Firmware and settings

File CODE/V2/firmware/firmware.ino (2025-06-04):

#define ENCODER1_PIN_A 2
#define ENCODER1_PIN_B 1
#define ENCODER2_PIN_A 11
#define ENCODER2_PIN_B 12
#define RESET_COUNT_ON_BOOT 1

#define LED_PIN 7
#define PWM_2 41
#define AIN_1 38
#define AIN_2 37
#define BIN_1 36
#define BIN_2 35
#define SLEEP_PIN 39

#define HEATER1_PIN 40  
#define HEATER2_PIN 41
#include <Arduino.h>
#include "motorConfig.h"
#include "tuning.h"
#include "bleCom.h"
#include "utils.h"


MotorPID motor1, motor2;
TuneSet<> tuning;


unsigned long previousMillis = 0;
const long interval = 100;  // interval in milliseconds

unsigned long previousMillis2 = 0;
const long interval2 = 500;
float freq1 = 0.0f, freq2 = 0.0f, phase1 = 0.0f, phase2 = 0.0f, amp1 = 0.0f, amp2 = 0.0f;
int8_t mode=0, mot_enabled=0, enable_heater1=0, enable_heater2=0, enable_auto=0;

void setup() {
    Serial.begin(115200);
    //while (!Serial);
    pinMode(HEATER1_PIN, OUTPUT);
    pinMode(HEATER2_PIN, OUTPUT);
    Serial.println("starting");
    // Initialize motor system with correct pin mapping
    motorInit(
        ENCODER1_PIN_A, ENCODER1_PIN_B,
        ENCODER2_PIN_A, ENCODER2_PIN_B,
        BIN_2, BIN_1,  // Motor 2 pins (BIN_2 = 35, BIN_1 = 36)
        AIN_2, AIN_1,  // Motor 1 pins (AIN_2 = 37, AIN_1 = 38)
        SLEEP_PIN,
        RESET_COUNT_ON_BOOT,
        3576 //revs per cycle
    );
    Serial.println("starting");
    // Initialize motor controllers with explicit configurations
    motor1.init({0, AIN_2, AIN_1, 3576}); // Motor 1 (num 0) uses AIN_2 & AIN_1
    motor2.init({1, BIN_2, BIN_1, 3576}); // Motor 2 (num 1) uses BIN_2 & BIN_1
    Serial.println("starting");
    // Tuning setup
    tuning.add("tar1", motor1.Setpoint);
    tuning.add("kp1", motor1.Kp);
    tuning.add("ki1", motor1.Ki);
    tuning.add("kd1", motor1.Kd);
    tuning.add("tar2", motor2.Setpoint);
    tuning.add("kp2", motor2.Kp);
    tuning.add("ki2", motor2.Ki);
    tuning.add("kd2", motor2.Kd);
    Serial.println("starting");
    motor1.setSetpointDeg(0.0f);
    motor2.setSetpointDeg(0.0f);

    Serial.println("Zeroing out motor 2");
    printEncoder();
    do {
    motor2.update();
    printEncoder();
    }
    while (motor2.Input!=0.0f);
    Serial.println("Zeroing out motor 1");
    printEncoder();
    do {
    motor1.update();
    printEncoder(); 
    }
    while (motor1.Input!=0.0f); // Wait for motors to be initialized
    Serial.println("motors zeroed");
    printEncoder();

    // Initialize BLE
    
    initBLE("azerty");
    // zero out encoders
    //motor1.startSinusoidalOscillation(0.15f, 180.0f);
    //motor2.startSinusoidalOscillation(0.15f, 180.0f);
    Serial.println("Setup complete");
}

void loop() {
    // Get BLE command
    unsigned long currentMillis = millis();
    unsigned long currentMillis2 = millis();
    tuning.readSerial();
    Command cmd = updateBLE();
    //debugPrint();
    
    if (cmd.isvalid) { //mode, input, mot, heat1, heat2, auto...freq,amp, ph, pos

    //enable heaters, outside because it needs unconstrained fast reading
    digitalWrite(HEATER1_PIN, static_cast<int8_t>(cmd.bytes[3]) ? HIGH : LOW); //replace with timed func 
    digitalWrite(HEATER2_PIN, static_cast<int8_t>(cmd.bytes[4]) ? HIGH : LOW); //replace with timed func
      if (static_cast<int8_t>(cmd.bytes[1])) // if input enabled
      {
        if (!static_cast<int8_t>(cmd.bytes[5])) //auto or move by joystick
        {
        //select motor
            MotorPID& motor = (static_cast<int8_t>(cmd.bytes[2]) == 0) ? motor1 : motor2;
            if (static_cast<int8_t>(cmd.bytes[2]) == 0) {
                freq1 = cmd.floats[0]; amp1 = cmd.floats[1]; phase1 =cmd.floats[2];
            }
            else {
                freq2 = cmd.floats[0]; amp2 = cmd.floats[1]; phase2 =cmd.floats[2];
            }
            //update vals //freq, amp, ph, pos
            
            if (static_cast<int8_t>(cmd.bytes[0])) // mode 1 do sinusoidal else do positional
              {
                if (motor.isOscillating() == 0) // if not oscillating
                {
                  motor.startSinusoidalOscillation(cmd.floats[0], cmd.floats[1], cmd.floats[2]);
                }
                else
                {
                    if (motor.oscillationFrequency!=cmd.floats[0]){
                        motor.setOscillationFrequency(cmd.floats[0]);
                    }
                    
                    if (motor.oscillationAmplitude!=cmd.floats[1]){
                        motor.setOscillationAmplitude(cmd.floats[1]);
                    }
                    
                    if (motor.oscillationPhase!=cmd.floats[2]){
                        motor.setOscillationPhase(cmd.floats[2]);
                    }
                    
                }
              }
              else
              {
                motor.stopSinusoidalOscillation();
                motor.goTo(int(cmd.floats[3]));
              }

            Serial.println("Valid Packet Received:");
            Serial.print("Bytes: ");
            for (int i = 0; i < BYTE_OBJECTS_LEN; i++) {
                int8_t inp=static_cast<int8_t>(cmd.bytes[i]);
                Serial.printf("%d ", inp);
            }
            Serial.println();
            Serial.print("Floats: ");
            for (int i = 0; i < FLOAT_OBJECTS_LEN; i++) {
                Serial.println(cmd.floats[i], 3);  // Print floats with precision
            }
            //motor1.setOscillationPhase(cmd.floats[1]);
            //motor2.setOscillationPhase(cmd.floats[0]);
          }
          else //auto mode
          {
            float x=mapfloat(float(static_cast<int8_t>(cmd.bytes[6])), -128, 127, -5, 5);
            float y=mapfloat(float(static_cast<int8_t>(cmd.bytes[7])), -128, 127, -5, 5);
            if (motor1.isOscillating() == 0) // if not oscillating
                {
                  motor1.startSinusoidalOscillation(freq1, amp1, phase1);
                }
            if (motor2.isOscillating() == 0) // if not oscillating
                {
                  motor2.startSinusoidalOscillation(freq2, amp2, phase2);
                }

                if (motor1.oscillationFrequency!=x){
                  motor1.setOscillationFrequency(x);
                  }
                if (motor2.oscillationFrequency!=y){
                  motor2.setOscillationFrequency(y);
                  }

            

          }
      }
    }


    static unsigned long lastSend = 0;
    if(millis() - lastSend > 30) {
        lastSend = millis();
        
        // Create sample data (position and velocity)
        int32_t dataToSend[] = {
            static_cast<int32_t>(motor1.Input),
            static_cast<int32_t>(motor1.Setpoint),
            static_cast<int32_t>(motor2.Input),
            static_cast<int32_t>(motor2.Setpoint)
        };
        
        bleSendIntegers(dataToSend);
    }

    motor1.update();
    motor2.update();

    // Handle command based on type
    // switch(cmd.cmd) {
    //     case 't':  // Target position
    //         motor1.Setpoint += cmd.value;
    //         break;
    //     case 'y':  // Target position
    //         motor1.Setpoint -= cmd.value;
    //         break;
    //     case 'p':  // Update Kp
    //         motor2.Setpoint += cmd.value;
    //         break;
    //     case 'o':  // Update Kp
    //         motor2.Setpoint -= cmd.value;
    //         break;
    //     case 'q':  // Predefined oscillation profile
    //         if(cmd.value == 0) {
    //             // Set to 90° phase (π/2 radians), 1Hz, 30° amplitude
    //             motor1.setOscillationPhase(PI);
    //             motor1.setOscillationFrequency(1.0f);
    //             motor1.setOscillationAmplitude(30.0f);
    //             motor2.setOscillationPhase(0);
    //             motor2.setOscillationFrequency(1.0f);
    //             motor2.setOscillationAmplitude(30.0f);
    //         }
    //         cmd.cmd=0;
    //         break;
    //     case 'a':  // Predefined oscillation profile
    //         if(cmd.value == 0) {
    //             // Set to 90° phase (π/2 radians), 1Hz, 30° amplitude
    //             motor1.setOscillationPhase(0.0f);
    //             motor1.setOscillationFrequency(0.25f);
    //             motor1.setOscillationAmplitude(180.0f);
    //             motor2.setOscillationPhase(0.0f);
    //             motor2.setOscillationFrequency(0.25f);
    //             motor2.setOscillationAmplitude(180.0f);
    //         }
    //         cmd.cmd=0;
    //         break;
    //     // Add more command handlers as needed
    // }
    
    // Update both motors
     if(motor1.isOscillating()) {
        // Update motor (oscillation is handled in update())
        motor1.update();
    }
    if(motor2.isOscillating()) {
        // Update motor (oscillation is handled in update())
        motor2.update();
    }

    // Serial print statements remain unchanged
    if (currentMillis - previousMillis >= interval) {
        previousMillis = currentMillis;
        //motor1.update();
        //motor2.update();
        debugPrint();
    }

    if (currentMillis2 - previousMillis2 >= interval2) {
        previousMillis2 = currentMillis2;
        //motor1.update();
        //blePrintf("%d,%d\n",motor1.Setpoint,motor2.Setpoint);
    }
    
    //delay(10);
}


void debugPrint()
{
    Serial.print(motor1.Setpoint); Serial.print("\t");
    Serial.print(motor1.Input);    Serial.print("\t");
    Serial.print(motor1.Output);   Serial.print("\t");
    Serial.print(motor1.Kp);       Serial.print("\t");
    Serial.print(motor1.Ki);       Serial.print("\t");
    Serial.print(motor1.Kd);       Serial.print("\t");

    Serial.print(motor2.Setpoint); Serial.print("\t");
    Serial.print(motor2.Input);    Serial.print("\t");
    Serial.print(motor2.Output);   Serial.print("\t");
    Serial.print(motor2.Kp);       Serial.print("\t");
    Serial.print(motor2.Ki);       Serial.print("\t");
    Serial.println(motor2.Kd);
}

void printEncoder()
{
  Serial.print(motor1.Setpoint); Serial.print("\t");
  Serial.print(motor1.Input);    Serial.print("\t");
  Serial.print(motor2.Setpoint); Serial.print("\t");
  Serial.println(motor2.Input);  
}


void updateHardware() 
{
  
}

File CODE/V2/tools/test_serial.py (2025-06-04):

import sys
import csv
import serial
from serial.tools import list_ports
from functools import partial
from PyQt5.QtWidgets import (QApplication, QMainWindow, QWidget, QVBoxLayout, 
                            QSlider, QLabel, QHBoxLayout, QGroupBox, QMessageBox,
                            QPushButton, QComboBox, QFileDialog)
from PyQt5.QtCore import QThread, pyqtSignal, pyqtSlot, Qt, QTimer, QElapsedTimer
from PyQt5.QtGui import QFont
import pyqtgraph as pg
import numpy as np
from datetime import datetime

# Configuration
DEFAULT_PORT = 'COM6'
BUFFER_SIZE = 50
SEND_DELAY_MS = 500
SETTLING_THRESHOLD = 6
DEBUG = False

# Parameter ranges
PARAM_RANGES = {
    'tar': (-41720, 41720),
    'kp': (0, 15),
    'ki': (0, 40),
    'kd': (-1, 15.0)
}

# Dark Theme
DARK_PALETTE = {
    'background': "#2D2D2D",
    'text': "#FFFFFF",
    'accent': "#3498DB",
    'secondary': "#2ECC71",
    'highlight': "#F1C40F",
    'warning': "#E74C3C",
    'plot_bg': "#1E1E1E",
    'slider_handle': "#000000"
}

STYLE_SHEET = f"""
    QWidget {{
        background-color: {DARK_PALETTE['background']};
        color: {DARK_PALETTE['text']};
        font-family: Segoe UI;
    }}
    QGroupBox {{
        border: 2px solid {DARK_PALETTE['accent']};
        border-radius: 5px;
        margin-top: 1ex;
        padding-top: 12px;
    }}
    QGroupBox::title {{
        subcontrol-origin: margin;
        left: 10px;
        color: {DARK_PALETTE['accent']};
    }}
    QSlider::groove:vertical {{
        background: {DARK_PALETTE['plot_bg']};
        width: 12px;
        border-radius: 6px;
    }}
    QSlider::handle:vertical {{
        background: {DARK_PALETTE['slider_handle']};
        border: 2px solid {DARK_PALETTE['accent']};
        height: 24px;
        width: 24px;
        margin: -8px -8px;
        border-radius: 12px;
    }}
    QPushButton {{
        background-color: {DARK_PALETTE['accent']};
        color: {DARK_PALETTE['text']};
        border: none;
        padding: 8px 16px;
        border-radius: 4px;
        font-size: 14px;
    }}
    QPushButton:hover {{
        background-color: #2980b9;
    }}
    QComboBox {{
        background: {DARK_PALETTE['plot_bg']};
        color: {DARK_PALETTE['text']};
        padding: 4px;
        min-width: 120px;
    }}
"""

class SerialWorker(QThread):
    data_received = pyqtSignal(list)
    error_occurred = pyqtSignal(str)

    def __init__(self, port, baud_rate):
        super().__init__()
        self.port = port
        self.baud_rate = baud_rate
        self.ser = None
        self.running = False

    def run(self):
        self.running = True
        try:
            self.ser = serial.Serial(self.port, self.baud_rate, timeout=0.1)
            while self.running:
                if self.ser.in_waiting > 0:
                    raw_line = self.ser.readline()
                    try:
                        line = raw_line.decode().strip()
                        if DEBUG:
                            print(f"Received: {line}")
                        if line:
                            parts = list(map(float, line.split('\t')))
                            if len(parts) == 12:
                                self.data_received.emit(parts)
                    except Exception as e:
                        continue
        except Exception as e:
            self.error_occurred.emit(str(e))
        finally:
            if self.ser and self.ser.is_open:
                self.ser.close()

    def send_command(self, command):
        if self.ser and self.running:
            try:
                self.ser.write(f"{command}\n".encode())
                if DEBUG:
                    print(f"Sent: {command}")
            except Exception as e:
                self.error_occurred.emit(str(e))

    def stop(self):
        self.running = False
        self.wait()

class MotorControlPanel(QWidget):
    def __init__(self, motor_id, color):
        super().__init__()
        self.motor_id = motor_id
        self.color = color
        self.slider_values = {'tar': 0, 'kp': 0, 'ki': 0, 'kd': 0}
        self.slider_timers = {}
        self.settling_timer = QElapsedTimer()
        self.settling_time_ms = None
        self.current_target = None
        self.sliders_initialized = False
        
        self.init_ui()
        self.init_slider_timers()

    def init_ui(self):
        layout = QVBoxLayout(self)
        layout.setContentsMargins(15, 15, 15, 15)
        
        # Title
        title = QLabel(f"MOTOR {self.motor_id}")
        title.setStyleSheet(f"font-size: 24px; color: {self.color};")
        layout.addWidget(title, alignment=Qt.AlignCenter)

        # Control Sliders
        sliders_group = QGroupBox("PID CONTROLS")
        sliders_layout = QHBoxLayout()
        
        slider_params = [
            ('tar', 'Target', *PARAM_RANGES['tar'], self.color),
            ('kp', 'Kp', *PARAM_RANGES['kp'], DARK_PALETTE['text']),
            ('ki', 'Ki', *PARAM_RANGES['ki'], DARK_PALETTE['text']),
            ('kd', 'Kd', *PARAM_RANGES['kd'], DARK_PALETTE['text'])
        ]

        self.sliders = {}
        for param, label, min_val, max_val, color in slider_params:
            group = QWidget()
            vbox = QVBoxLayout(group)
            vbox.setAlignment(Qt.AlignCenter)
            
            param_label = QLabel(label)
            param_label.setStyleSheet(f"color: {color}; font-size: 16px;")
            
            value_label = QLabel("0.00")
            value_label.setStyleSheet(f"color: {color}; font-size: 14px;")
            
            slider = QSlider(Qt.Vertical)
            slider.setRange(0, 1000)
            slider.valueChanged.connect(partial(
                self.on_slider_change, 
                param, min_val, max_val, value_label
            ))
            slider.setStyleSheet(f"""
                QSlider::handle:vertical {{
                    background: {color};
                    border: 2px solid {DARK_PALETTE['accent']};
                }}
            """)
            
            vbox.addWidget(param_label)
            vbox.addWidget(value_label)
            vbox.addWidget(slider)
            sliders_layout.addWidget(group)
            self.sliders[param] = (value_label, slider)

        sliders_group.setLayout(sliders_layout)
        layout.addWidget(sliders_group)
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

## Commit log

2025-04-03 add files to git
    [0.6_7_8_32 compressedSLDPRT.SLDPRT, 0.6_7_8_32.SLDPRT, 0.6_7_8_32_semi_compressed.SLDPRT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]
2025-04-03 added older files and additional work done
    [20 mm 3.2 screw.3MF, 20 mm 3.3 screw.3MF, 20 mm 3.4 screw.3MF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]
2025-04-03 added kinematics
2025-04-14 foot bending rendering assembly
    [0.6_7_8_32 compressedSLDPRT.SLDPRT, 9mm o ring.SLDPRT, back body 25mm 2.SLDPRT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]
2025-04-14 updated mold
2025-04-25 modified vertebrae to fit better
    [foot mold v4.SLDPRT, resin cup.SLDPRT, vertebrae v4.SLDPRT]
2025-06-04 gliding version
    [Cep.SLDDRW, Cep.SLDPRT, Cev 1.SLDDRW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]
2025-06-04 added things
    [SCS8UU.SLDPRT, Shf 8mm.SLDPRT]
2025-06-11 square circle
    [SCS8UU.SLDPRT, Shf 8mm.SLDPRT, circular-to-square.SLDASM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]
2025-06-11 fan changes and sim
    [Resetka.SLDPRT, steel sheet.SLDPRT]
2025-06-19 updated measurement thingie
    [0.6_7_8_32 compressedSLDPRT.SLDPRT, 0.6_7_8_32.SLDPRT, 0.6_7_8_32_semi_compressed.SLDPRT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]
